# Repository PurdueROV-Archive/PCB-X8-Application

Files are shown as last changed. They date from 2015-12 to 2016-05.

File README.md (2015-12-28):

# PCB-X8-Application
The board that contains mission specific electronics

# LED driver overview
- Controlled by Texas Instruments LM3409HV Buck Controller
- Steps down Application board 12V power to 6V, 0.5A max
- Output current adjustable via PWM to allow for LED dimming
- Drives two high power white LEDs

# Main considerations taken in design of the board:
	- No ground plane or traces opposite the inductor avoid effects of eddy currents
	- Input capacitors located as close to the chip power pins on the same layer
	- Drain of PFET connected as close as possible to power inductor, with minimal trace area
	- Place output capacitor close to the inductor
	- At least 4 thermal vias located under the buck controller thermal pad for heat dissipation	
	- Isolate small signal ground (IC ground) from the power ground
	- Minimise the use of vias for the power ground
	- Isolate noise-causing components (diode, inductor, PWM signal) away from other components
	- In particular, below are the recommendations for designing the feedback route. However the design of our particular driver makes them somewhat irrelevant:
		a). Feedback terminal of IC which inputs feedback signal, is normally designed with high impedance. Output of this terminal and
		resistor crossover network must be connected with short wire.
		b). Part which detects the output voltage must be connected after output capacitor or at both ends of output capacitor.
		c). Wiring the resistor-divider circuit nearby and parallel, makes it better for noise tolerance.
		d). Draw wire far away from switching node of inductor and diode. Do not wire directly below the inductor and diode, and not
		parallel to power supply line. Multilayer board must be also wired in the same way. 
	- Proper land pattern of power components to minimize impedance: (Application Notes 136, Page 7)
		http://cds.linear.com/docs/en/application-note/an136f.pdf

(recommendations drawn from: http://rohmfs.rohm.com/en/products/databook/applinote/ic/power/switching_regulator/converter_pcb_layout_appli-e.pdf)

# Possible changes/improvements:
	- decrease the board area
	
# Thoughts:
	- The board schematic was based off the 'Typical Applications' under section 8.2 of the Buck Controller datasheet. For some reason that design does not have a output capacitor, unlike standard buck controller designs
	- The design mentioned above also uses a different feedback system compared to the standard; namely it only uses 1 resistor instead of 2

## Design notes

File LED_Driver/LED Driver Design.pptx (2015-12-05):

## LED Diver (Buck Converter)

- Controlled by Texas Instruments LM3409HV Buck Controller
- Steps down Application board 12V power to 6V, 0.5A max
- Output current adjustable via PWM to allow for LED dimming
- Drives two high power white LEDs

## Schematic

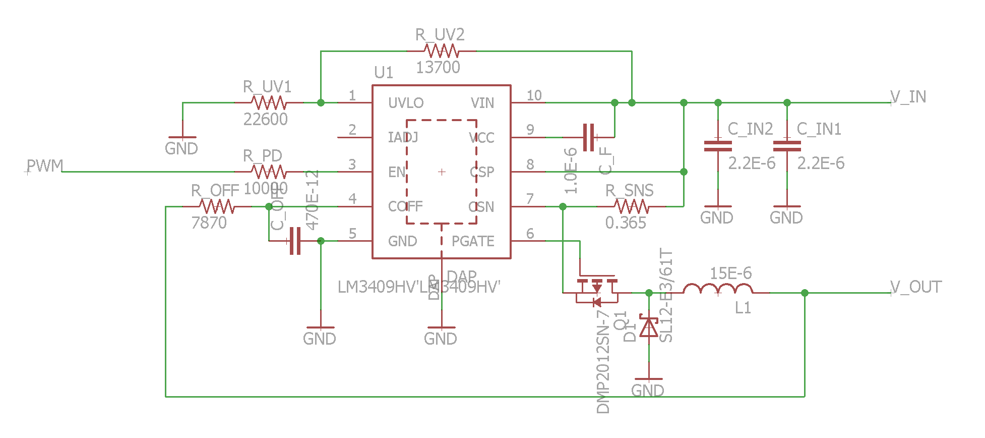
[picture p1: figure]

## Board

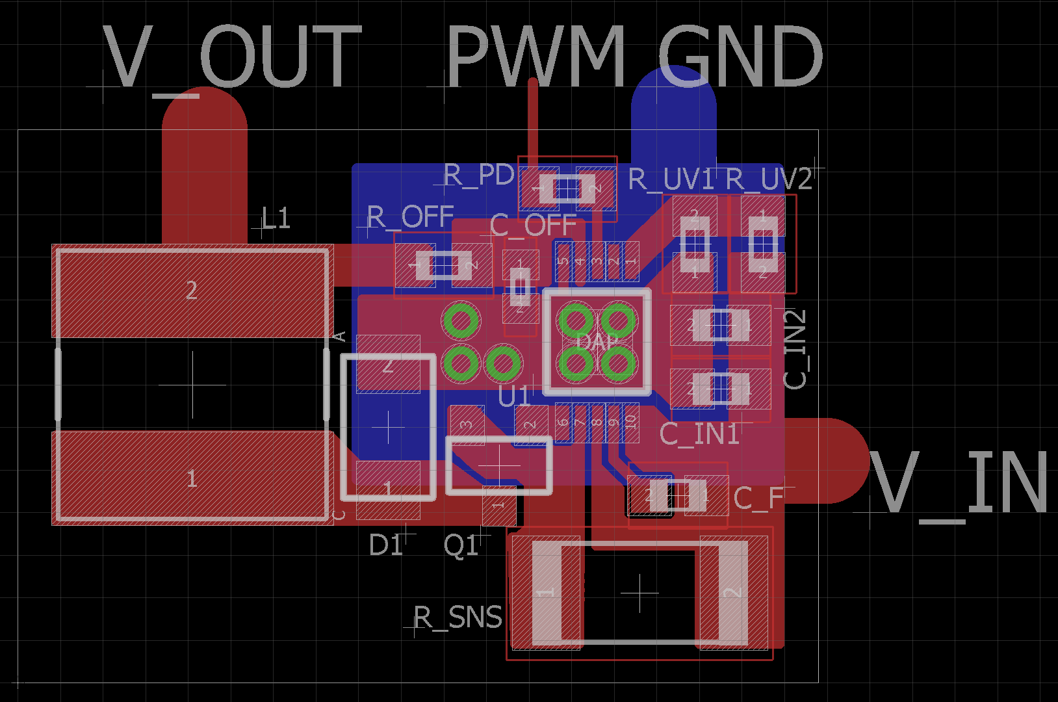
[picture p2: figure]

## Board (cont.)

Main considerations taken in design of the board:
- No ground plane or traces opposite the inductor avoid effects of eddy currents
- Input capacitors located as close to the chip power pins on the same layer
- Drain of PFET connected as close as possible to power inductor, with minimal trace area
- Place output capacitor close to the inductor
- At least 4 thermal vias located under the buck controller thermal pad for heat dissipation
- Isolate small signal ground (IC ground) from the power ground

## Board (cont.)

- Minimise the use of vias for the power ground
- Isolate noise-causing components (diode, inductor, PWM signal) away from other components
- In particular, there recommendations for designing the feedback route. However the design of our particular driver makes them somewhat irrelevant.
- Proper land pattern of power components to minimize impedance: (Application Notes 136, Page 7)
http://cds.linear.com/docs/en/application-note/an136f.pdf

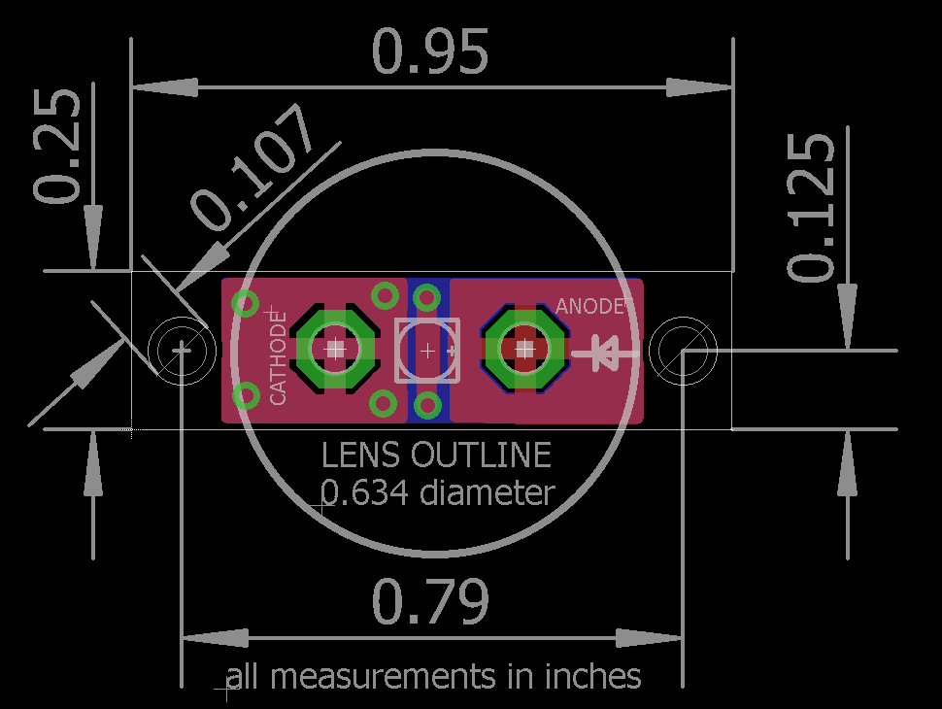
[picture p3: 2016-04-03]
LED Board/LED Board V2 Dimensions.png

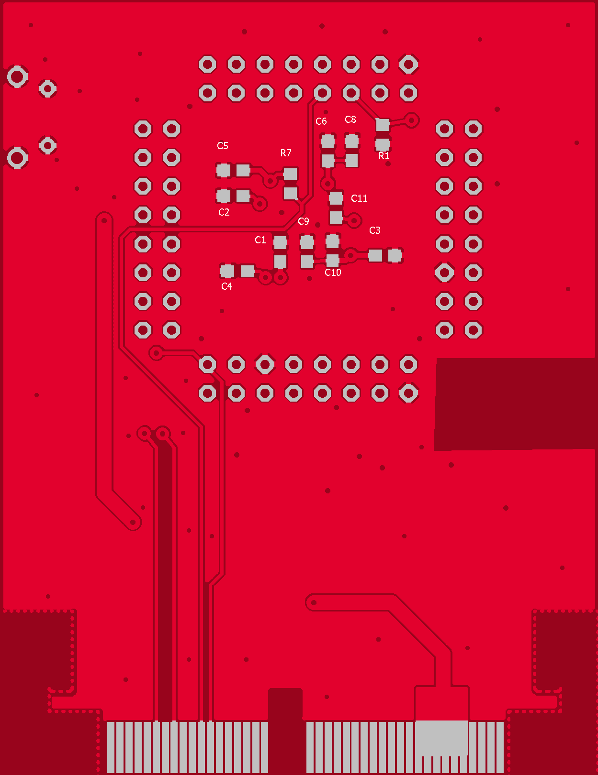
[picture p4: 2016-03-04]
Application Board/eagleUp/eagleUp_Application_board_bottom.png

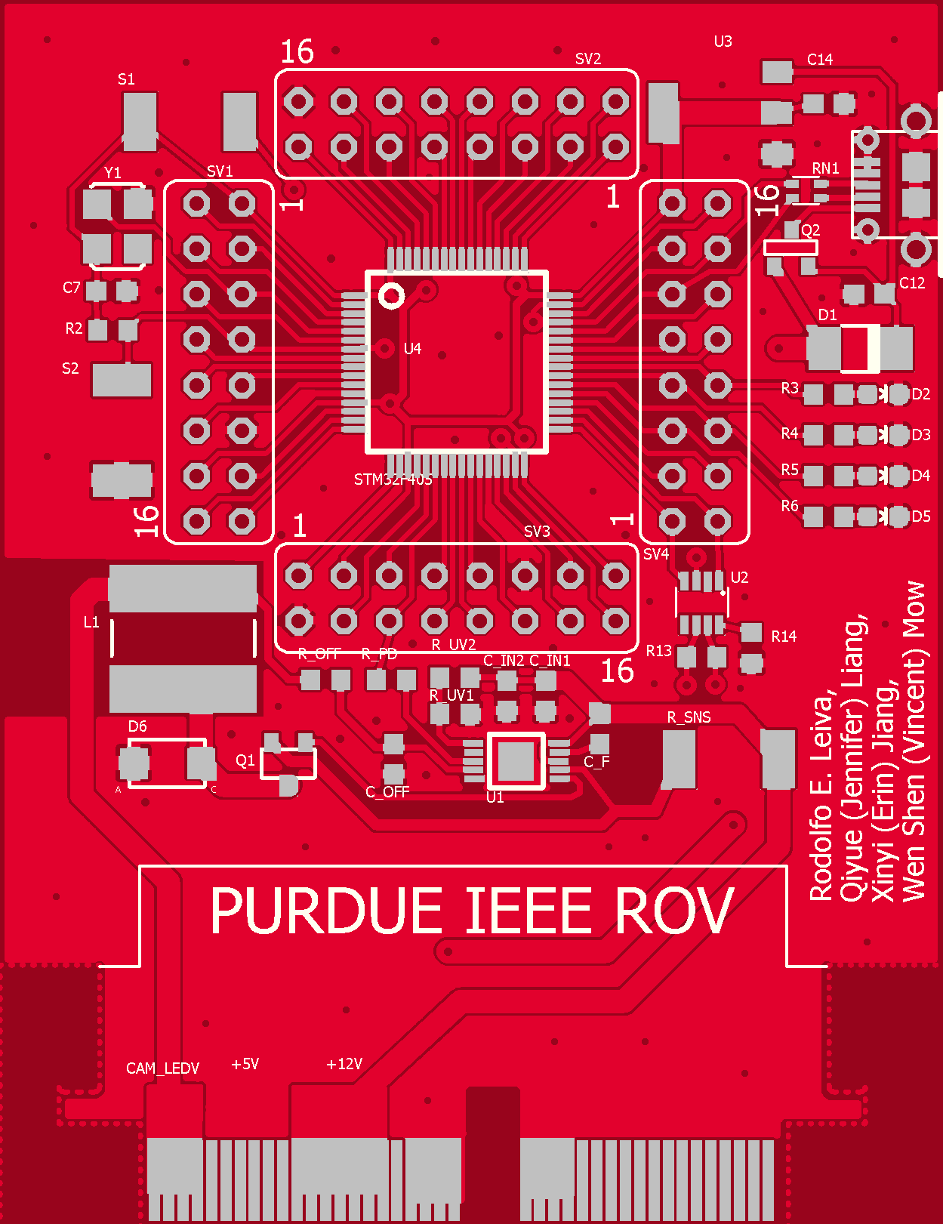
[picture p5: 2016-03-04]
Application Board/eagleUp/eagleUp_Application_board_top.png

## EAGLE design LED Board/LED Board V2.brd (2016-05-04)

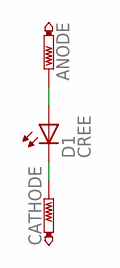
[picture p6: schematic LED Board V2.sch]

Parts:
ANODE: PTR1PAD1-20; P1-20
CATHODE: PTR1PAD1-20; P1-20
D1: CREE; CREE-XLAMP-XM-L

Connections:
ANODE: ANODE.TP, D1.A, D1.A@1 (A)
CATHODE: CATHODE.TP, D1.C, D1.C1 (C), D1.C@1 (C)

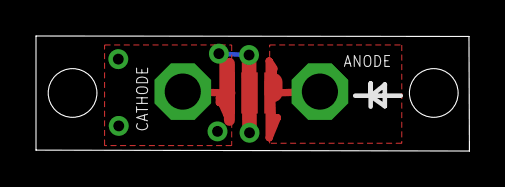
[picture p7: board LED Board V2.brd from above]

Board: 2 copper layers, 24.1 x 6.4 mm, 3 parts (0 on the bottom side), 2 nets.

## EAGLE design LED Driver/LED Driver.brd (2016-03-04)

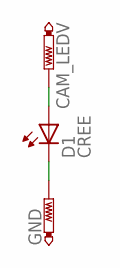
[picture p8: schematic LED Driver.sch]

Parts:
CAM_LEDV: PTR1PAD1-20; P1-20
D1: CREE; CREE-XLAMP-XM-L
GND: PTR1PAD1-20; P1-20

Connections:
CAM_LEDV: CAM_LEDV.TP, D1.A, D1.A@1 (A)
GND: D1.C, D1.C1 (C), D1.C@1 (C), GND.TP

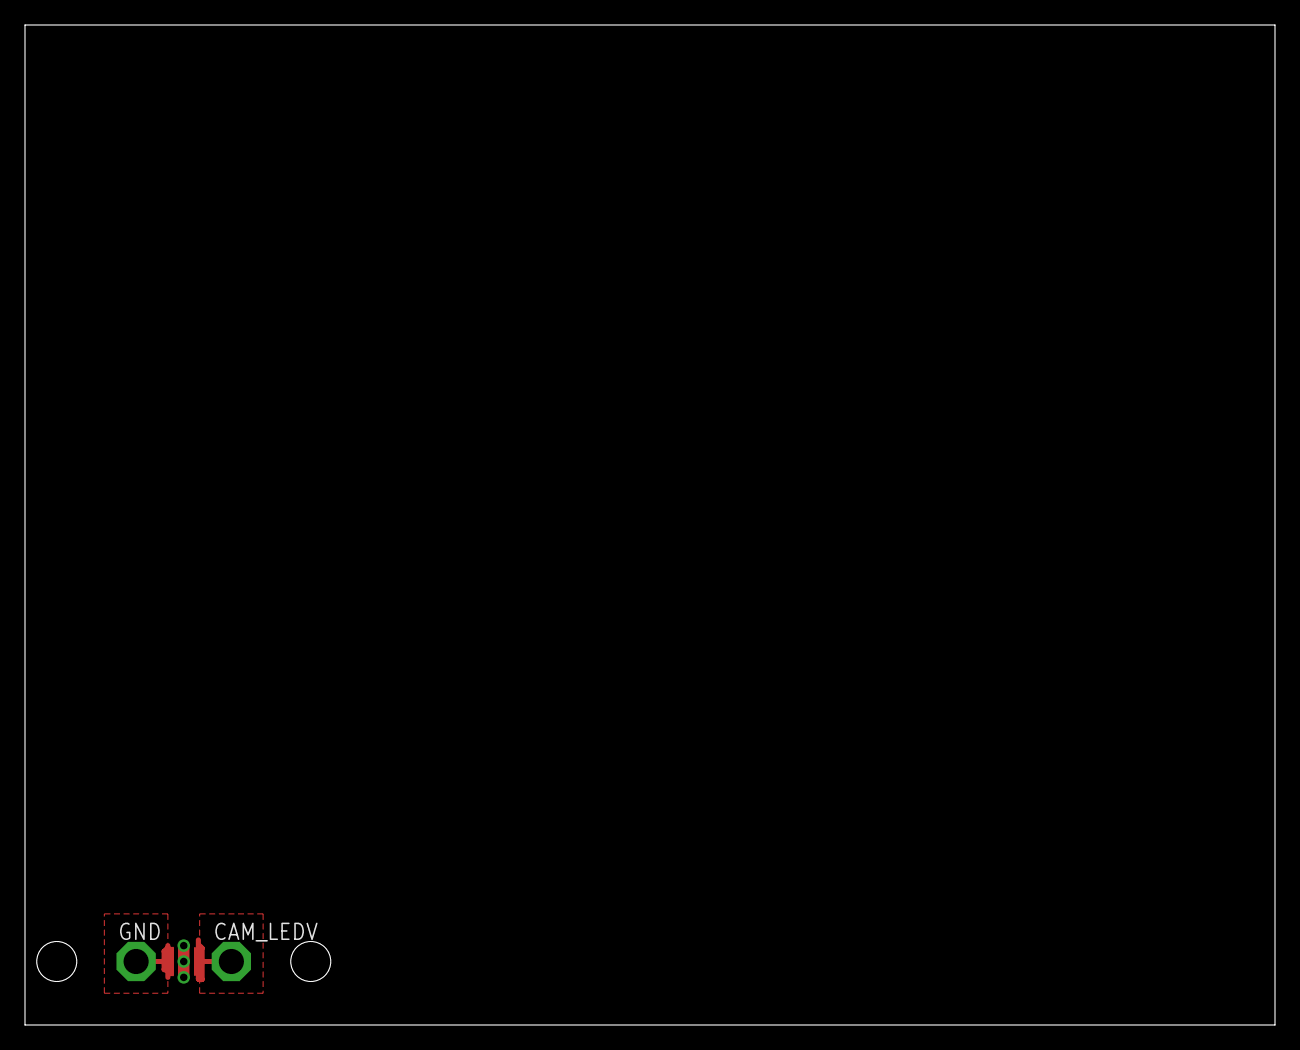
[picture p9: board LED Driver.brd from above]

Board: 2 copper layers, 100.0 x 80.0 mm, 3 parts (0 on the bottom side), 2 nets.

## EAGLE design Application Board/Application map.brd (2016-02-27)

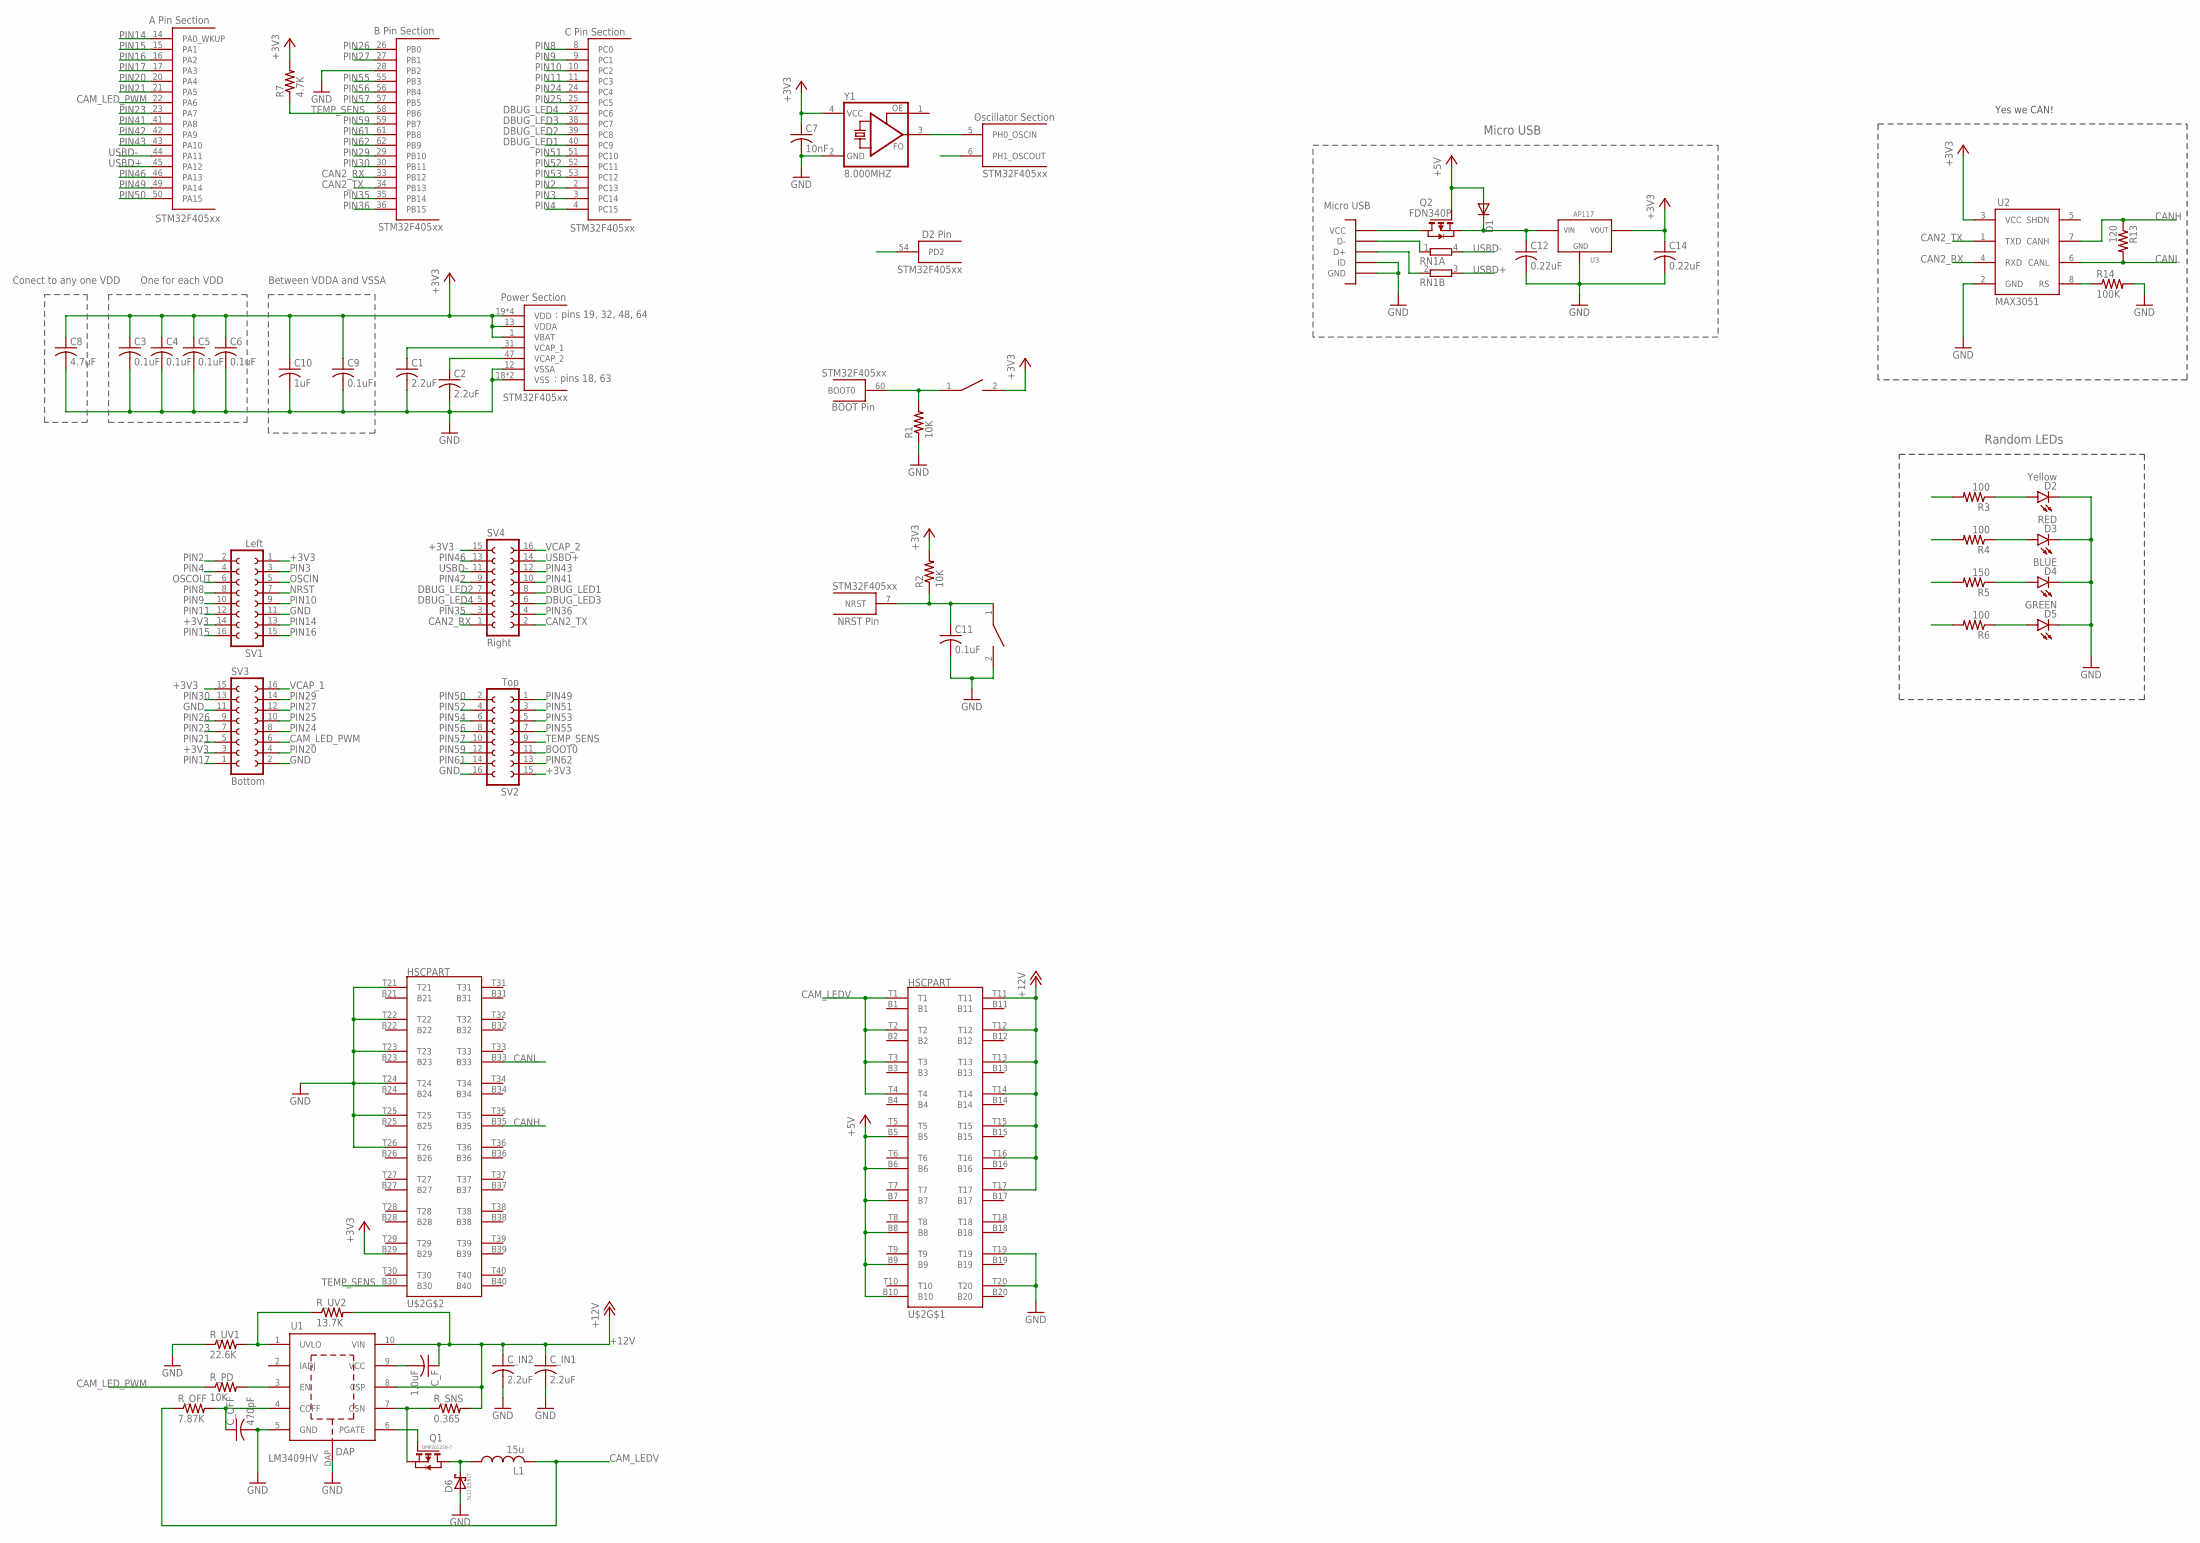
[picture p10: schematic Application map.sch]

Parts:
C1, C2: 2.2uF; C0603
C3, C4, C5, C6, C9, C11: 0.1uF; C0603
C7: 10nF; C0603
C8: 4.7uF; C0603
C10: 1uF; C0603
C12, C14: 0.22uF; C0603
C_F: 1.0uF; C0603
C_IN1, C_IN2: 2.2uF; C0603
C_OFF: 470pF; C0603
D1: DIODE-DO-214AC; DO-214AC
D2: Yellow; LED-0603
D3: RED; LED-0603
D4: BLUE; LED-0603
D5: GREEN; LED-0603
D6: SL12-E3/61T
L1: 15u; SRN8040
Q1: DMP2012SN-7
Q2: FDN340P; SOT-23
R1, R2: 10K; R0603
R3, R4, R6: 100; R0603
R5: 150; R0603
R7: 4.7K; R0603
R13: 120; R0603
R14: 100K; R0603
RN1: 2R-NEXBV4V; EXBV4V
R_OFF: 7.87K; R0603
R_PD: 10K; R0603
R_SNS: 0.365; R2512
R_UV1: 22.6K; R0603
R_UV2: 13.7K; R0603
S1: BOOT; SW_2512
S2: RESET; SW_2512
SV1: Left; FE08-2
SV2: Top; FE08-2
SV3: Bottom; FE08-2
SV4: Right; FE08-2
U1: LM3409HV; VSSOP-10
U2: MAX3051; SOT23-8L
U3: U3; SOT223
U4: STM32F405; LQFP64
U5: MICROUSB; MICRO_B
U$2: HSCPART; HSC8-40PINOUUT
Y1: 8.000MHZ; ASF

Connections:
+3V3: C3.1, C4.1, C5.1, C6.1, C7.1, C8.1, C9.1, C10.1, C14.1, R2.2, R7.2, S1.2, SV1.1, SV1.14, SV2.15, SV3.3, SV3.15, SV4.15, U2.3 (VCC), U3.TAB (VOUT), U3.VOUT, U4.1 (VBAT), U4.13 (VDDA), U4.19 (VDD), U4.32 (VDD), U4.48 (VDD), U4.64 (VDD), U$2.B29, Y1.4 (VCC)
+5V: D1.A, Q2.3 (G), U$2.B5, U$2.B6, U$2.B7, U$2.B8, U$2.B9, U$2.B10
+12V: C_F.1, C_IN1.1, C_IN2.1, R_SNS.2, R_UV2.2, U1.8 (CSP), U1.10 (VIN), U$2.T11, U$2.T12, U$2.T13, U$2.T14, U$2.T15, U$2.T16, U$2.T17
BOOT0: R1.2, S1.1, SV2.11, U4.60 (BOOT0)
CAM_LEDV: L1.2, R_OFF.1, U$2.T1, U$2.T2, U$2.T3, U$2.T4
CAM_LED_PWM: R_PD.1, SV3.6, U4.22 (PA6)
CAN2_RX: SV4.1, U2.4 (RXD), U4.33 (PB12)
CAN2_TX: SV4.2, U2.1 (TXD), U4.34 (PB13)
CANH: R13.1, U2.7 (CANH), U$2.B35
CANL: R13.2, U2.6 (CANL), U$2.B33
DBUG_LED1: R3.2, SV4.8, U4.40 (PC9)
DBUG_LED2: R4.2, SV4.7, U4.39 (PC8)
DBUG_LED3: R5.2, SV4.6, U4.38 (PC7)
DBUG_LED4: R6.2, SV4.5, U4.37 (PC6)
GND: C1.2, C2.2, C3.2, C4.2, C5.2, C6.2, C7.2, C8.2, C9.2, C10.2, C11.2, C12.2, C14.2, C_IN1.2, C_IN2.2, C_OFF.2, D2.C, D3.C, D4.C, D5.C, D6.2 (A), R1.1, R14.2, R_UV1.1, S2.2, SV1.11, SV2.16, SV3.2, SV3.11, U1.5 (GND), U1.DAP, U2.2 (GND), U3.GND, U4.12 (VSSA), U4.18 (VSS), U4.28 (PB2), U4.63 (VSS), U5.GND1 (GND), U5.GND2 (GND), U5.GND3 (GND), U5.GND4 (GND), U5.GND7 (GND), U5.GND8 (GND), U5.P4 (ID), U5.P5 (GND), U$2.T19, U$2.T20, U$2.T21, U$2.T22, U$2.T23, U$2.T24, U$2.T25, U$2.T26, Y1.2 (GND)
L1: D6.1 (C), L1.1, Q1.1 (D)
unnamed: RN1.1, U5.P2 (D-)
unnamed: R_UV1.2, R_UV2.1, U1.1 (UVLO)
unnamed: C_OFF.1, R_OFF.2, U1.4 (COFF)
unnamed: C_F.2, U1.9 (VCC)
unnamed: Q1.3 (S), R_SNS.1, U1.7 (CSN)
unnamed: R_PD.2, U1.3 (EN)
unnamed: Q1.2 (G), U1.6 (PGATE)
unnamed: RN1.2 (1), U5.P3 (D+)
unnamed: Q2.1 (D), U5.P1 (VCC)
unnamed: C12.1, D1.C, Q2.2 (S), U3.VIN
unnamed: D2.A, R3.1
unnamed: D3.A, R4.1
unnamed: D4.A, R5.1
unnamed: D5.A, R6.1
unnamed: R14.1, U2.8 (RS)
NRST: C11.1, R2.1, S2.1, SV1.7, U4.7 (NRST)
OSCIN: SV1.5, U4.5 (PH0_OSCIN), Y1.3 (FO)
OSCOUT: SV1.6, U4.6 (PH1_OSCOUT)
PIN2: SV1.2, U4.2 (PC13)
PIN3: SV1.3, U4.3 (PC14)
PIN4: SV1.4, U4.4 (PC15)
PIN8: SV1.8, U4.8 (PC0)
PIN9: SV1.10, U4.9 (PC1)
PIN10: SV1.9, U4.10 (PC2)
PIN11: SV1.12, U4.11 (PC3)
PIN14: SV1.13, U4.14 (PA0_WKUP)
PIN15: SV1.16, U4.15 (PA1)
PIN16: SV1.15, U4.16 (PA2)
PIN17: SV3.1, U4.17 (PA3)
PIN20: SV3.4, U4.20 (PA4)
PIN21: SV3.5, U4.21 (PA5)
PIN23: SV3.7, U4.23 (PA7)
PIN24: SV3.8, U4.24 (PC4)
PIN25: SV3.10, U4.25 (PC5)
PIN26: SV3.9, U4.26 (PB0)
PIN27: SV3.12, U4.27 (PB1)
PIN29: SV3.14, U4.29 (PB10)
PIN30: SV3.13, U4.30 (PB11)
PIN35: SV4.3, U4.35 (PB14)
PIN36: SV4.4, U4.36 (PB15)
PIN41: SV4.10, U4.41 (PA8)
PIN42: SV4.9, U4.42 (PA9)
PIN43: SV4.12, U4.43 (PA10)
PIN46: SV4.13, U4.46 (PA13)
PIN49: SV2.1, U4.49 (PA14)
PIN50: SV2.2, U4.50 (PA15)
PIN51: SV2.3, U4.51 (PC10)
PIN52: SV2.4, U4.52 (PC11)
PIN53: SV2.5, U4.53 (PC12)
PIN54: SV2.6, U4.54 (PD2)
PIN55: SV2.7, U4.55 (PB3)
PIN56: SV2.8, U4.56 (PB4)
PIN57: SV2.10, U4.57 (PB5)
PIN59: SV2.12, U4.59 (PB7)
PIN61: SV2.14, U4.61 (PB8)
PIN62: SV2.13, U4.62 (PB9)
TEMP_SENS: R7.1, SV2.9, U4.58 (PB6), U$2.B30
USBD+: RN1.3 (2), SV4.14, U4.45 (PA12)
USBD-: RN1.4 (2), SV4.11, U4.44 (PA11)
VCAP_1: C1.1, SV3.16, U4.31 (VCAP_1)
VCAP_2: C2.1, SV4.16, U4.47 (VCAP_2)

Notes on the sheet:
: pins 19, 32, 48, 64
: pins 18, 63
Between VDDA and VSSA
One for each VDD
Conect to any one VDD
Micro USB
Yes we CAN!
Random LEDs

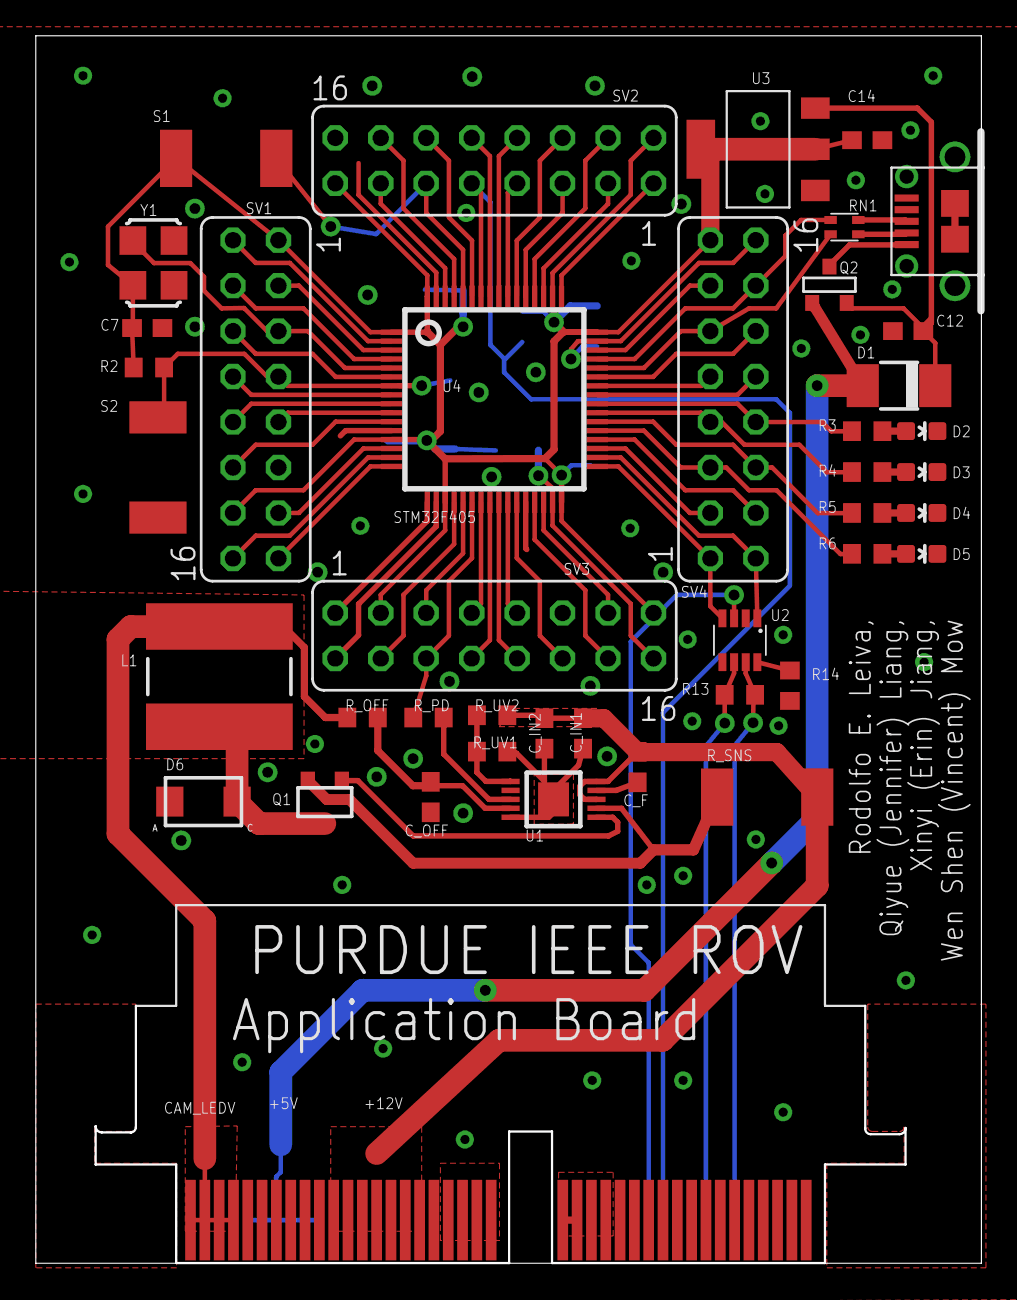
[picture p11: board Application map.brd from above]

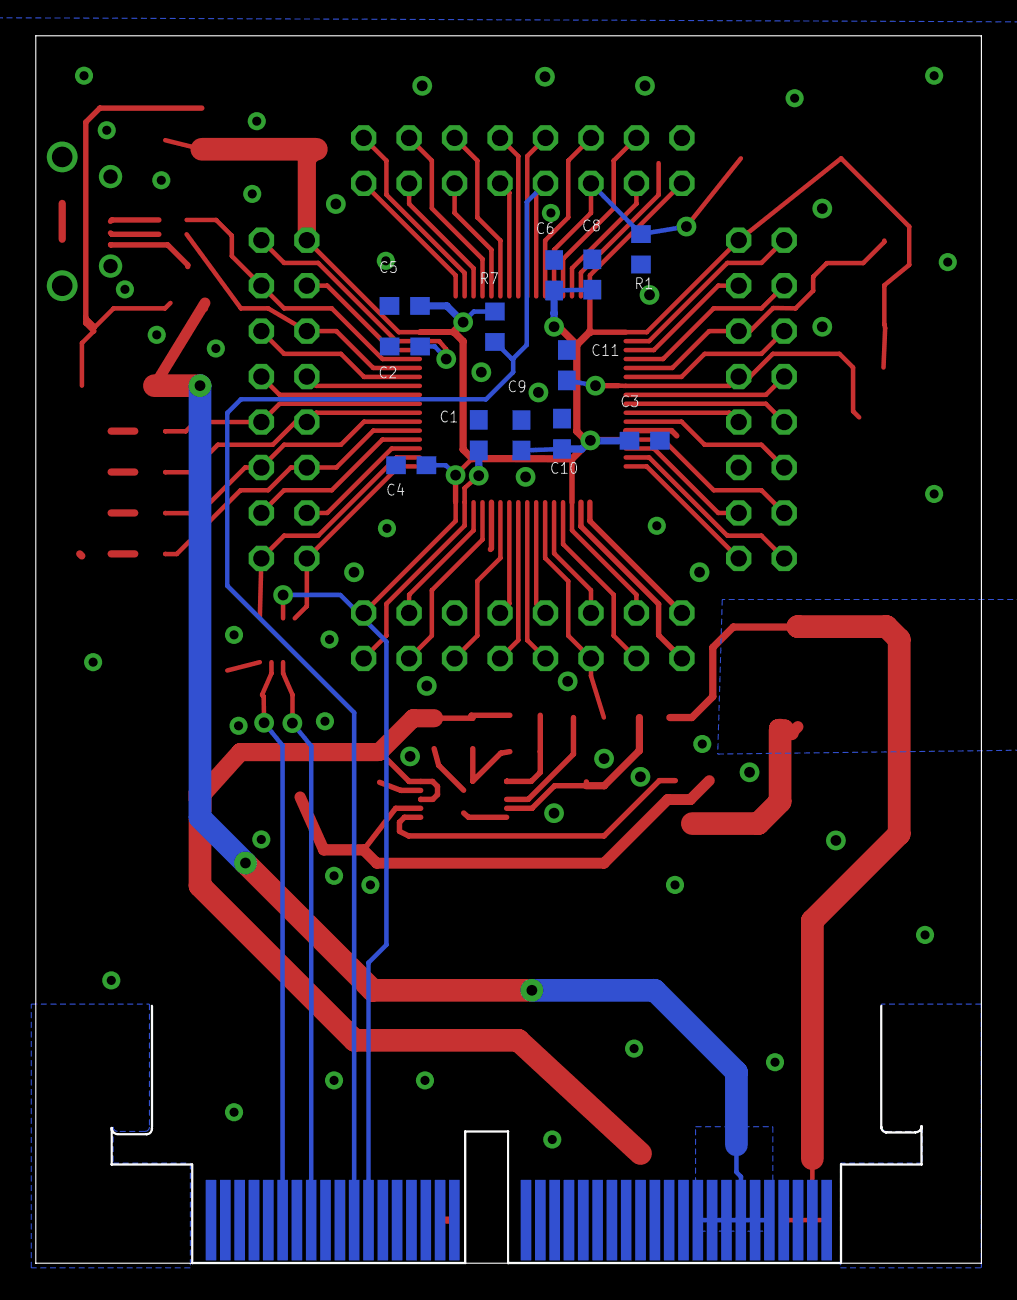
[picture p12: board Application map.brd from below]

Board: 2 copper layers, 52.8 x 68.6 mm, 54 parts (12 on the bottom side), 77 nets.

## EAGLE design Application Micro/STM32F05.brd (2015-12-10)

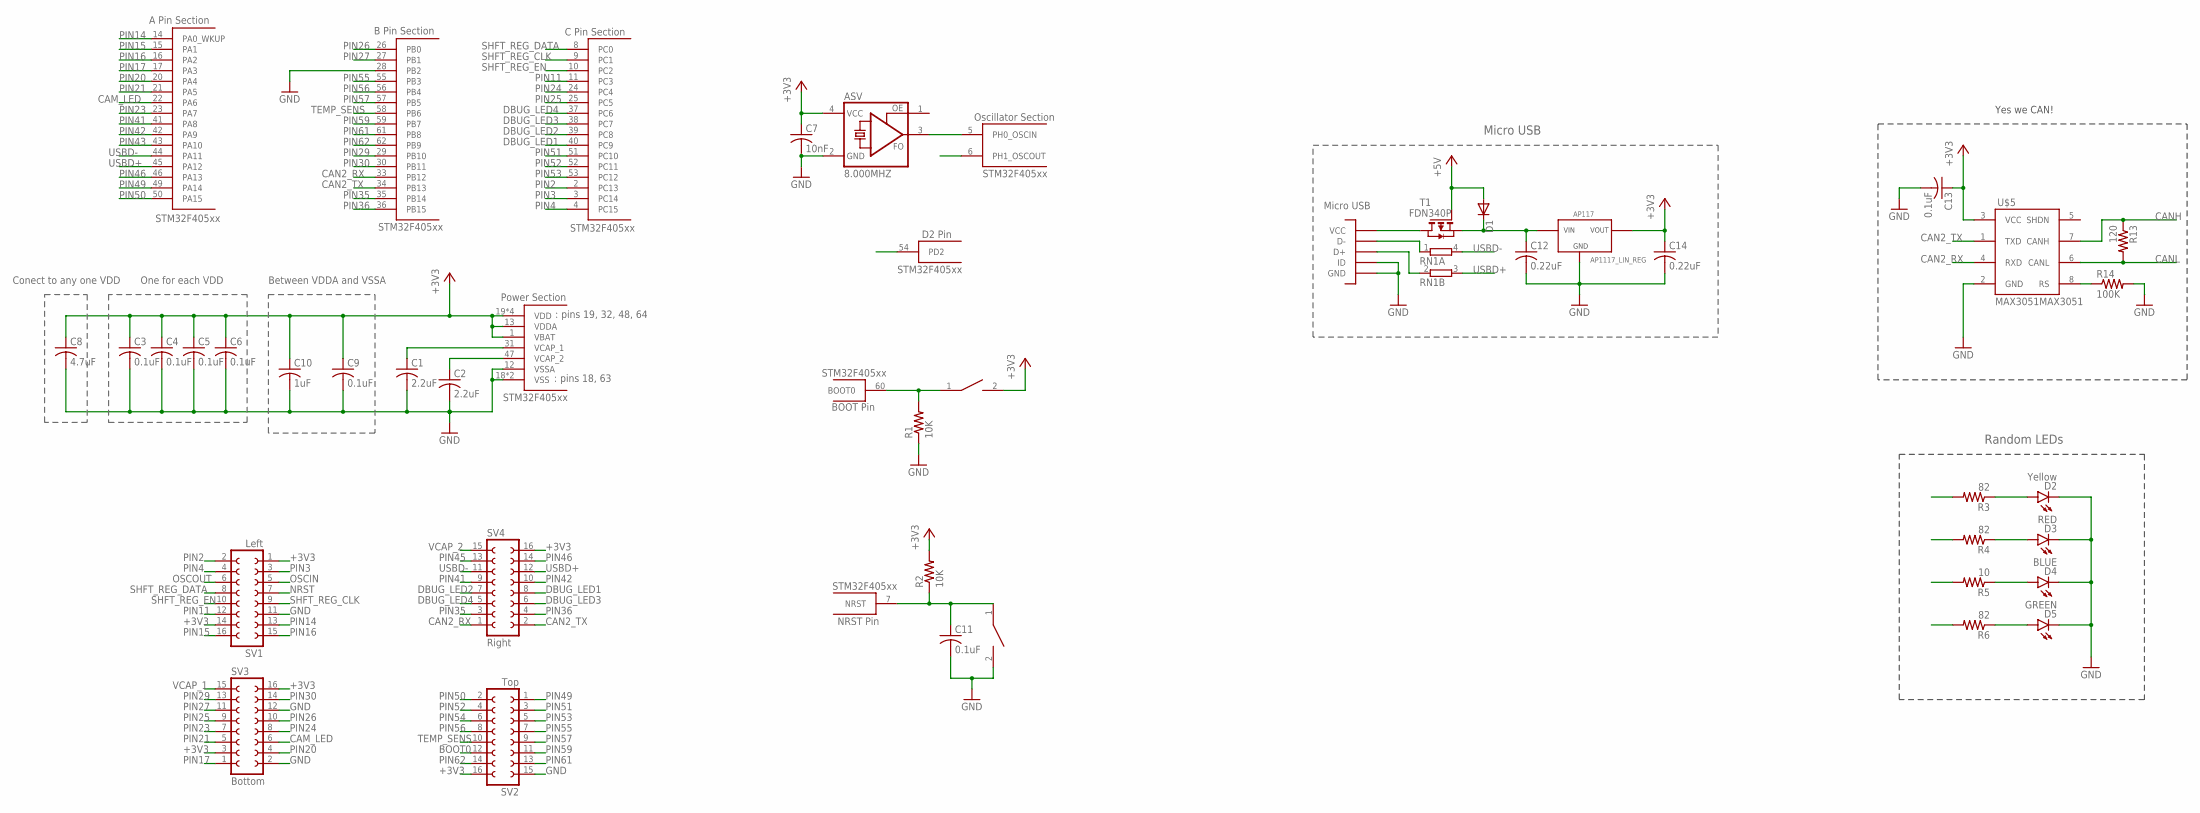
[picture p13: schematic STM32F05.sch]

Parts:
ASV: 8.000MHZ; ASF
C1, C2: 2.2uF; C0603
C3, C4, C5, C6, C9, C11, C13: 0.1uF; C0603
C7: 10nF; C0603
C8: 4.7uF; C0603
C10: 1uF; C0603
C12, C14: 0.22uF; C0603
D1: DIODE-DO-214AC; DO-214AC
D2: Yellow; LED-0603
D3: RED; LED-0603
D4: BLUE; LED-0603
D5: GREEN; LED-0603
R1, R2: 10K; R0603
R3, R4, R6: 82; R0603
R5: 10; R0603
R13: 120; R0603
R14: 100K; R0603
RN1: 2R-NEXBV4V; EXBV4V
SV1: Left; FE08-2
SV2: Top; FE08-2
SV3: Bottom; FE08-2
SV4: Right; FE08-2
T1: FDN340P; SOT-23
T2: AP1117_LIN_REG; SOT223
U$1: STM32F405; LQFP64
U$2, U$3: SWITCH; SW_2512
U$4: MICROUSB; MICRO_B
U$5: MAX3051MAX3051; SOT23-8L

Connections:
+3V3: ASV.4 (VCC), C3.1, C4.1, C5.1, C6.1, C7.1, C8.1, C9.1, C10.1, C13.1, C14.1, R2.2, SV1.1, SV1.14, SV2.16, SV3.3, SV3.16, SV4.16, T2.TAB (VOUT), T2.VOUT, U$1.1 (VBAT), U$1.13 (VDDA), U$1.19 (VDD), U$1.32 (VDD), U$1.48 (VDD), U$1.64 (VDD), U$2.2, U$5.3 (VCC)
+5V: D1.A, T1.3 (G)
BOOT0: R1.2, SV2.12, U$1.60 (BOOT0), U$2.1
CAM_LED: SV3.6, U$1.22 (PA6)
CAN2_RX: SV4.1, U$1.33 (PB12), U$5.4 (RXD)
CAN2_TX: SV4.2, U$1.34 (PB13), U$5.1 (TXD)
CANH: R13.1, U$5.7 (CANH)
CANL: R13.2, U$5.6 (CANL)
DBUG_LED1: R3.2, SV4.8, U$1.40 (PC9)
DBUG_LED2: R4.2, SV4.7, U$1.39 (PC8)
DBUG_LED3: R5.2, SV4.6, U$1.38 (PC7)
DBUG_LED4: R6.2, SV4.5, U$1.37 (PC6)
GND: ASV.2 (GND), C1.2, C2.2, C3.2, C4.2, C5.2, C6.2, C7.2, C8.2, C9.2, C10.2, C11.2, C12.2, C13.2, C14.2, D2.C, D3.C, D4.C, D5.C, R1.1, R14.2, SV1.11, SV2.15, SV3.2, SV3.12, T2.GND, U$1.12 (VSSA), U$1.18 (VSS), U$1.28 (PB2), U$1.63 (VSS), U$3.2, U$4.GND1 (GND), U$4.GND2 (GND), U$4.GND3 (GND), U$4.GND4 (GND), U$4.GND7 (GND), U$4.GND8 (GND), U$4.P4 (ID), U$4.P5 (GND), U$5.2 (GND)
unnamed: RN1.1, U$4.P2 (D-)
unnamed: RN1.2 (1), U$4.P3 (D+)
unnamed: T1.1 (D), U$4.P1 (VCC)
unnamed: C12.1, D1.C, T1.2 (S), T2.VIN
unnamed: D2.A, R3.1
unnamed: D3.A, R4.1
unnamed: D4.A, R5.1
unnamed: D5.A, R6.1
unnamed: R14.1, U$5.8 (RS)
NRST: C11.1, R2.1, SV1.7, U$1.7 (NRST), U$3.1
OSCIN: ASV.3 (FO), SV1.5, U$1.5 (PH0_OSCIN)
OSCOUT: SV1.6, U$1.6 (PH1_OSCOUT)
PIN2: SV1.2, U$1.2 (PC13)
PIN3: SV1.3, U$1.3 (PC14)
PIN4: SV1.4, U$1.4 (PC15)
PIN11: SV1.12, U$1.11 (PC3)
PIN14: SV1.13, U$1.14 (PA0_WKUP)
PIN15: SV1.16, U$1.15 (PA1)
PIN16: SV1.15, U$1.16 (PA2)
PIN17: SV3.1, U$1.17 (PA3)
PIN20: SV3.4, U$1.20 (PA4)
PIN21: SV3.5, U$1.21 (PA5)
PIN23: SV3.7, U$1.23 (PA7)
PIN24: SV3.8, U$1.24 (PC4)
PIN25: SV3.9, U$1.25 (PC5)
PIN26: SV3.10, U$1.26 (PB0)
PIN27: SV3.11, U$1.27 (PB1)
PIN29: SV3.13, U$1.29 (PB10)
PIN30: SV3.14, U$1.30 (PB11)
PIN35: SV4.3, U$1.35 (PB14)
PIN36: SV4.4, U$1.36 (PB15)
PIN41: SV4.9, U$1.41 (PA8)
PIN42: SV4.10, U$1.42 (PA9)
PIN43: U$1.43 (PA10)
PIN45: SV4.13
PIN46: SV4.14, U$1.46 (PA13)
PIN49: SV2.1, U$1.49 (PA14)
PIN50: SV2.2, U$1.50 (PA15)
PIN51: SV2.3, U$1.51 (PC10)
PIN52: SV2.4, U$1.52 (PC11)
PIN53: SV2.5, U$1.53 (PC12)
PIN54: SV2.6, U$1.54 (PD2)
PIN55: SV2.7, U$1.55 (PB3)
PIN56: SV2.8, U$1.56 (PB4)
PIN57: SV2.9, U$1.57 (PB5)
PIN59: SV2.11, U$1.59 (PB7)
PIN61: SV2.13, U$1.61 (PB8)
PIN62: SV2.14, U$1.62 (PB9)
SHFT_REG_CLK: SV1.9, U$1.9 (PC1)
SHFT_REG_DATA: SV1.8, U$1.8 (PC0)
SHFT_REG_EN: SV1.10, U$1.10 (PC2)
TEMP_SENS: SV2.10, U$1.58 (PB6)
USBD+: RN1.3 (2), SV4.12, U$1.45 (PA12)
USBD-: RN1.4 (2), SV4.11, U$1.44 (PA11)
VCAP_1: C1.1, SV3.15, U$1.31 (VCAP_1)
VCAP_2: C2.1, SV4.15, U$1.47 (VCAP_2)

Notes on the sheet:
: pins 19, 32, 48, 64
: pins 18, 63
Between VDDA and VSSA
One for each VDD
Conect to any one VDD
Micro USB
Yes we CAN!
Random LEDs

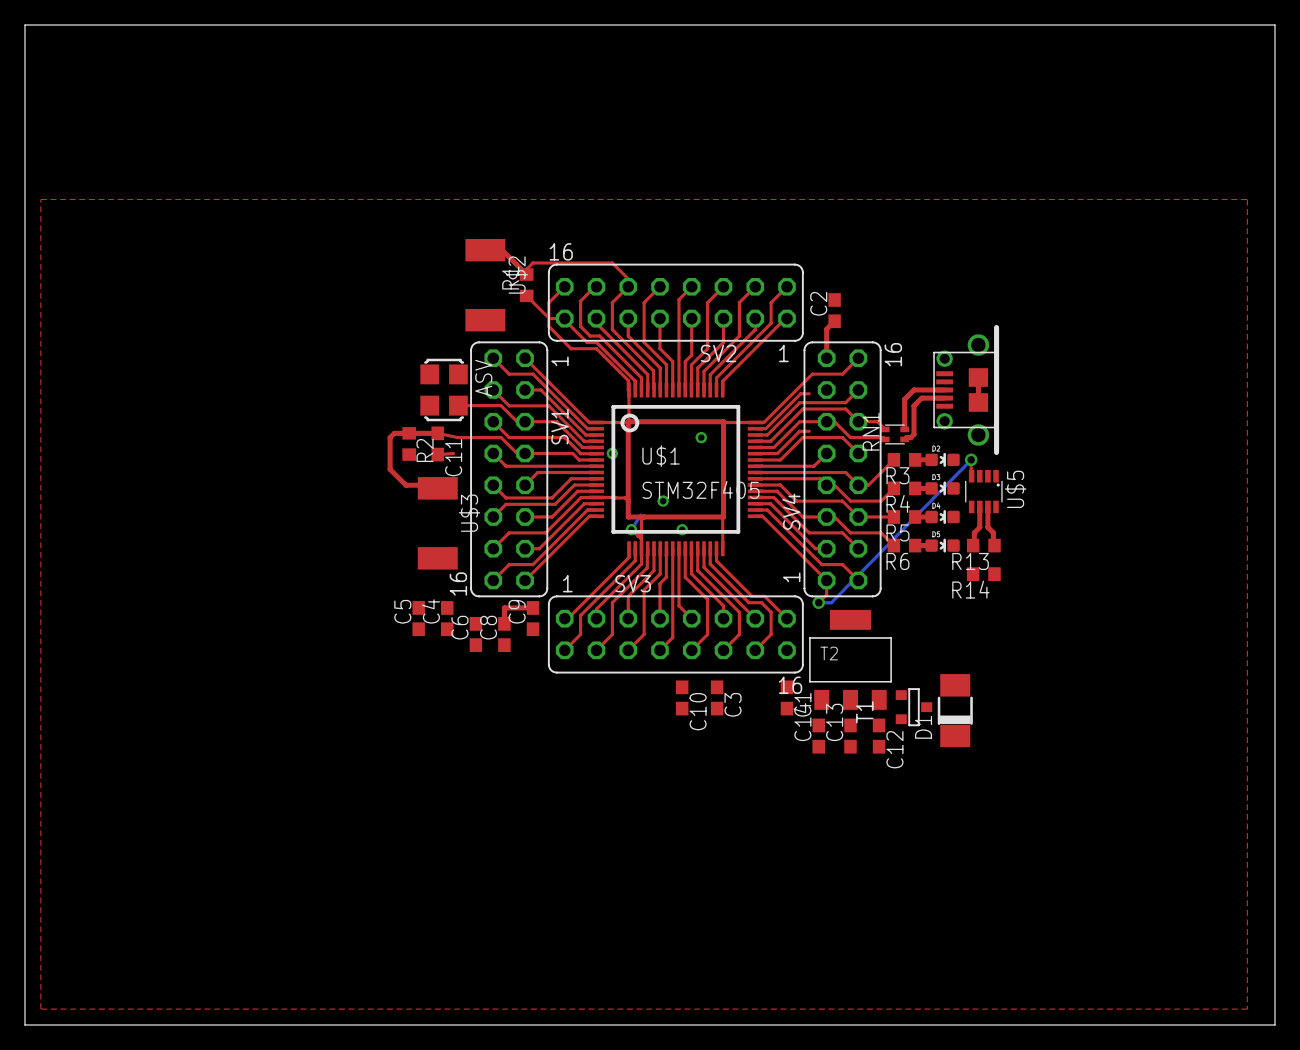
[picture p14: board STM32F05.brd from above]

Board: 2 copper layers, 100.0 x 80.0 mm, 40 parts (1 on the bottom side), 67 nets.

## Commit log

2015-11-07 Added Can Schematic
    Can Schematic without CAN Controller
    [CAN Circuit.sch]
2015-11-07 Added CAN folder
    [CAN Circuit.sch]
2015-11-19 Added STM32F05 microcontroller shematic
    Not finished yet.
    [STM32F05.sch]
2015-11-19 Changes 11/18/2015
    Continued schematic design.
    Created PCB file
    [STM32F05.brd, STM32F05.sch]
2015-11-21 Updated application micro board
    [STM32F05.brd, STM32F05.sch]
2015-11-25 Continued work on application micro
    Added circuitry for bi-directional linear regulator. Named some pins.
    [STM32F05.brd, STM32F05.sch]
2015-11-25 Added last parts to application board microcontroller.
    Added the linear regulator, finished as much of schematic as we can for
    now. *I think* Now all that's left is deciding what pins do what.
    [STM32F05.brd, STM32F05.sch]
2015-12-02 Connected the programming pins
    [STM32F05.brd, STM32F05.sch]
2015-12-03 LED Drivers (Buck Converter)
    Here are two different board layouts for the buck converter. The first
    version was done without any consideration for proper buck converter PCB
    design. The second version takes into account design recommendations as
    specified in:
    http://rohmfs.rohm.com/en/products/databook/applinote/ic/power/switching_regulator/converter_pcb_layout_appli-e.pdf
    and http://cds.linear.com/docs/en/application-note/an136f.pdf. However
    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
    [LEDDriver.brd, LEDDriver.sch]
2015-12-05 Minor changes to trace placement in LED Driver v2
    Minor changes to trace placement in LED Driver v2
    [LEDDriver.brd, LEDDriver.sch]
2015-12-05 Updated LED Driver README
2015-12-05 Updated LED driver README
    Added component land pattern considerations
2015-12-05 Added the LED driver PPT
    Used for the design review
2015-12-05 Made LED Driver v1 obsolete
    Refer to LED Driver v2 instead
    [LEDDriver.brd, LEDDriver.sch]
2015-12-05 Minor trace adjustments
    Adjustments updated to eagle board file and powerpoint file
    [LEDDriver.brd]
2015-12-05 Application Micro V2
    Removed shift regulator (for I2C), named pins, connected can circuit to
    can schematic.
    [STM32F05_V2.brd, STM32F05_V2.sch]
2015-12-07 Changes to traces and fills
    Changed non-thermal fills to thermals/traces for most non-power
    components. Main trace sizes used to route those components are 0.025"
    and 0.012"
    [LEDDriver.brd]
2015-12-10 change the value of LED resistors
    [STM32F05_V2.sch]
2015-12-10 Started Routing
    [STM32F05_V2.brd]
2015-12-10 combined application board parts into one board
    [Application.brd, Application.sch]
2015-12-28 Fixed some bad git practices
    [LEDDriver.brd, LEDDriver.sch, STM32F05.brd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]
2015-12-31 Moved capacitors around
    [Application.brd, Application.sch]
2015-12-31 Fixed all the routing on the microcontroller.
    [Application.brd, Application.sch]
2015-12-31 added order of board input voltage and signals
    [Application.brd, Application.sch]
2016-01-01 Rearranged components, including LED driver.
    Not finished, still need to fix LED driver and route the remaining
    connector lines.
    [Application.brd, Application.sch]
2016-01-07 updated stm... microcontroller to the updated version
    organized order of output lines. Still not complete.
    [Application.brd, Application.sch]
2016-01-07 Fixed output voltages and signal paths, added connector
    [Application.brd, Application.sch]
2016-01-08 Fixed up some wiring
    [Application.brd, Application.sch]
2016-01-08 fixed some connections
    Have been trying to solve some problems with some polygons and haven't
    been able to fix other issues.
    [Application.brd, Application.sch]
2016-01-09 fixed ground planes and added vias
    [Application.brd]
2016-01-09 update 1/8/2016
    cant remember what I changed. What ever it was must have been minor.
    looks like a change in via position and sizes and a few other minor
    adjustments.
    [Application.brd]
2016-01-09 Cleaned up some of the traces
    [Application.brd]
2016-01-14 Added The U Type +3V3 Wire
    [Application.brd]
2016-01-15 Update 1/15/16 4:50pm
    Added Temp_Sens Pullup Resistor, connected remaining air wires, modified
    path of a few lines
    [Application.brd, Application.sch]
2016-01-15 Fixed some DLC Errors
    [Application.brd]
2016-01-16 Fixed some DRC errors?
    [Application.brd]
2016-01-16 Fixed All The DRC Errors Except The Dimension Errors
    [Application.brd]
2016-01-16 Board Layout Finished！
    [Application.brd, Application.sch]
2016-01-16 Added Designers names and "PURDUE IEEE ROV"
    [Application.brd, Application.sch]
2016-01-16 Changed some names, added vias
    [Application.brd, Application.sch]
2016-01-16 Added Gerber Files and Designers Aliases
    [Application.brd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]
2016-02-27 Update on changes since last push
    Can't remember everything I changed, but it was mostly reorganizing
    names.
    [Application map.brd, Application map.sch]
2016-02-27 Created LED Driver
    [LED Driver.brd, LED Driver.sch]
2016-03-04 board sketch up model update
2016-03-23 Updated LED board
    Ready for manufacturing
    [LED Board.brd, LED Board.sch]
2016-04-02 Added symbols to the LED board
    [LED Board.brd, LED Board.sch]
2016-04-03 Fixed dimensions of LED board
    Also added measurement documentation on board.
    Included png file of final board with measurements.
    [LED Board V2.brd, LED Board V2.sch]
2016-05-04 I don't know what got updated
    [LED Board V2.brd]

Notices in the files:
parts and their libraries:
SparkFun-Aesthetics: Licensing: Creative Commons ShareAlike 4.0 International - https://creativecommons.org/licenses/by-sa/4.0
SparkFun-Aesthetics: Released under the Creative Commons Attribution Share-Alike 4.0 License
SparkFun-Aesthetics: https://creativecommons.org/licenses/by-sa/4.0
